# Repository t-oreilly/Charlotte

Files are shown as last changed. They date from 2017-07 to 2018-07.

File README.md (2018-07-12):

# Charlotte
Charlotte - Light Reactive Drawing Robot

Charlotte is an interactive drawing robot that senses light and responds to it accordingly.
Download the build instructions and STL files to build your own robot. Once compleated, you will be able to change the behavior
of the robot by uploading different codes. Watch a video of the robot in action here https://vimeo.com/221069279

You can also download the project from instrucables @ https://www.instructables.com/id/Charlotte/

Charlotte was first made in a http://schoolofma.org/ workshop in 2015

Collaborators 

Abe -  http://hamoid.com/ 

Peter Kolski 

Yuri - www.yurishimaoka.org

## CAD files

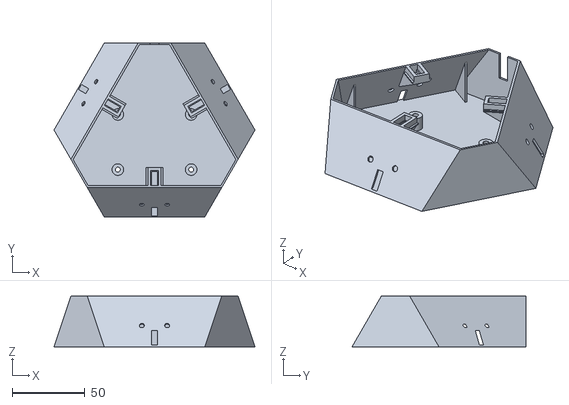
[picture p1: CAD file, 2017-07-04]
3::STL_/Body_1/mainBody_.stl
138.6 x 120.0 x 35.0

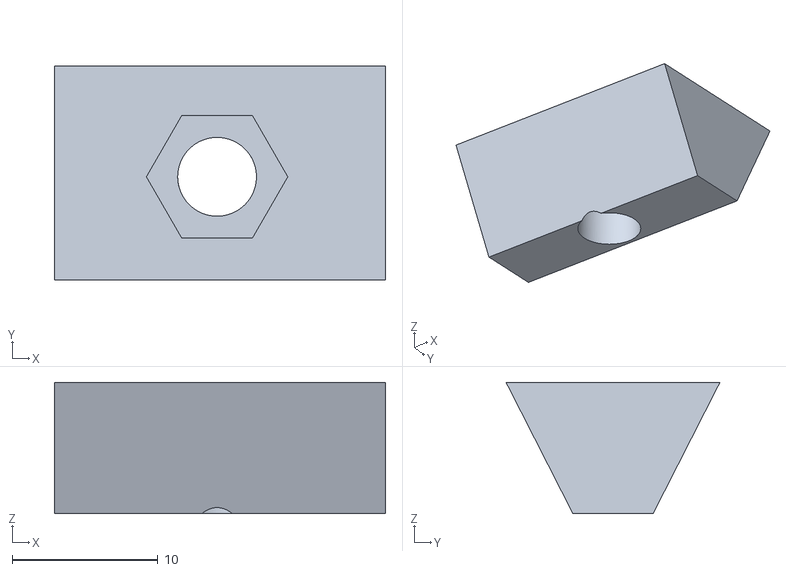
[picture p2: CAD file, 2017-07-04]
3::STL_/Body_1/servoWedge_.stl
22.7 x 14.7 x 9.00

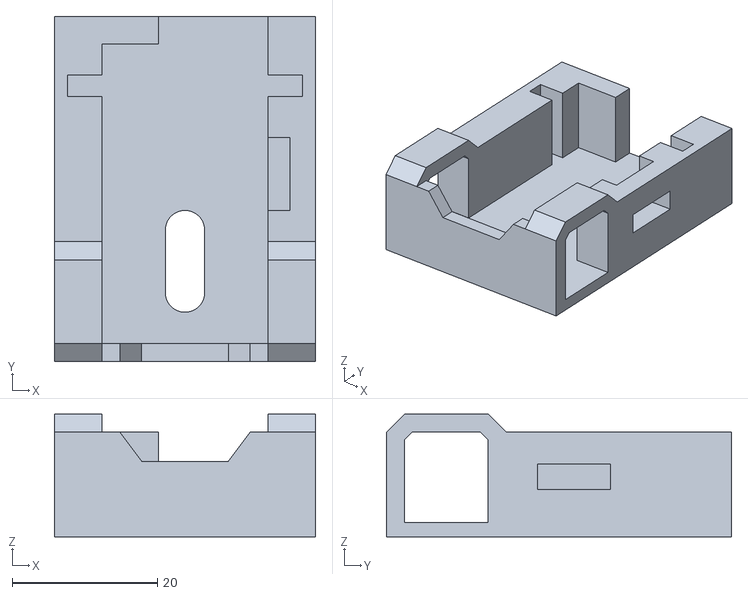
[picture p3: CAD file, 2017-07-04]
3::STL_/Body_1/servoHouseing_.stl
35.9 x 47.5 x 16.9

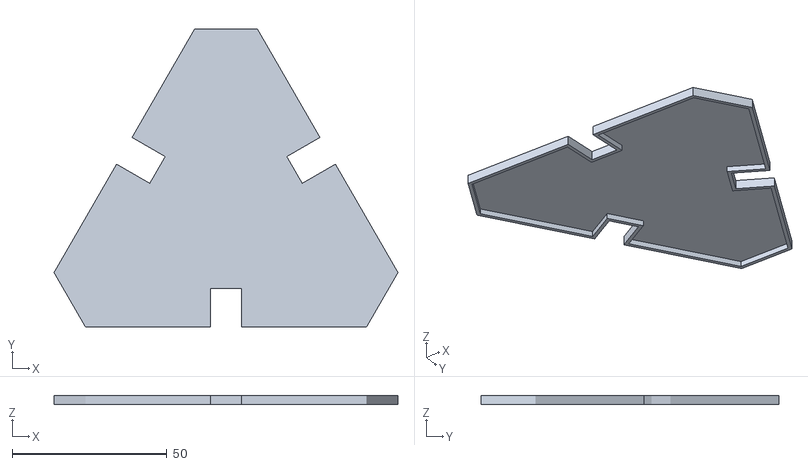
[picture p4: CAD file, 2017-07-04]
3::STL_/Body_1/bodyLid_.stl
111.3 x 96.4 x 3.00

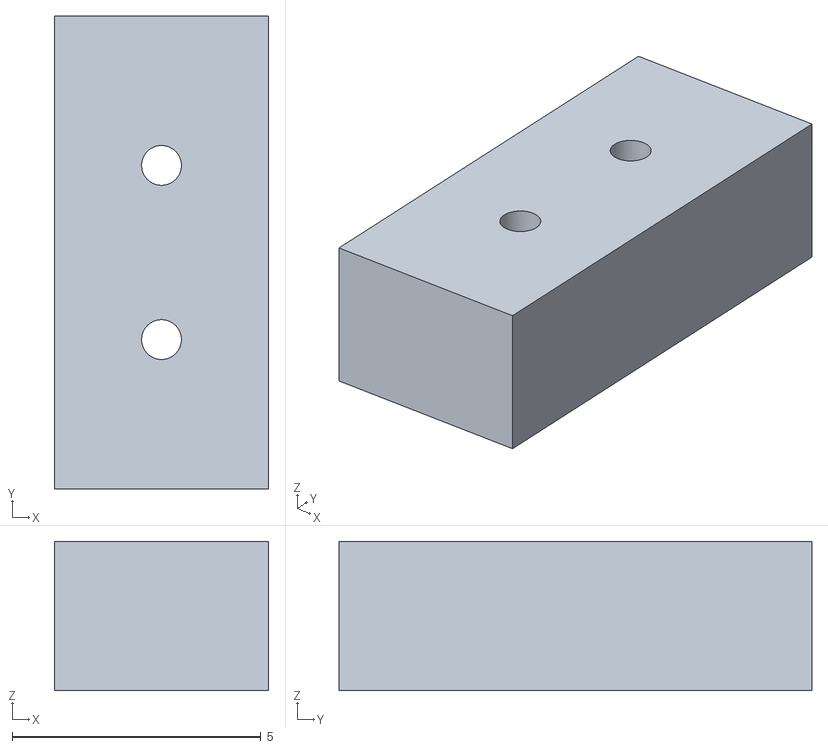
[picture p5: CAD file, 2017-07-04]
3::STL_/Body_1/sensorHouse_.stl
4.30 x 9.50 x 3.00

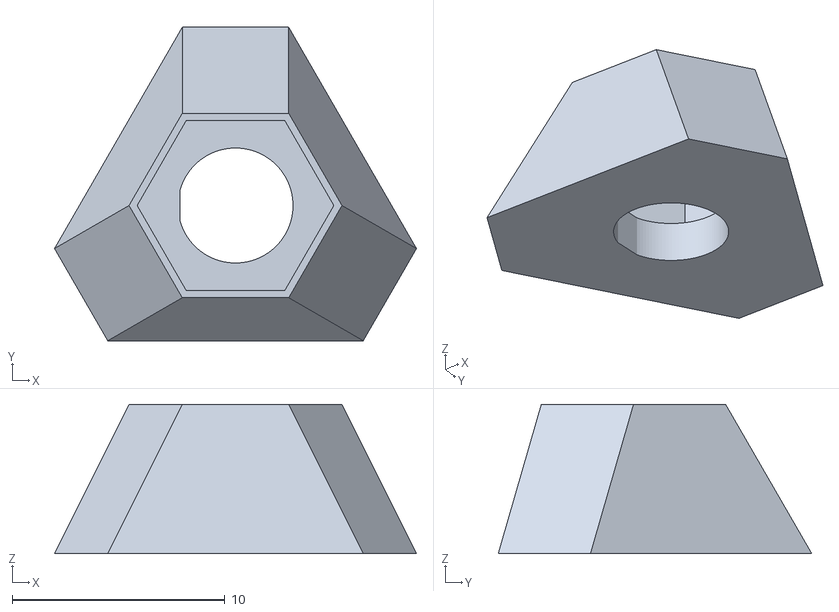
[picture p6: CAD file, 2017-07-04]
3::STL_/Body_1/boltHouse_.stl
17.0 x 14.7 x 7.00

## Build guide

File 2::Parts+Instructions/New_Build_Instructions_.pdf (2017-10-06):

Intro
Tools Needed
Parts Needed
Soldering

1
2
3
4
5
6
7

Callibration
Assembly
Play

### What if you could download a Product?

INTRO

The rise in popularity of 3D printing and the Internet becoming ubiquitous has prompted many speculations about how the democratization of manufacturing and the free sharing of information will affect our environments. Charlotte, as well as being a functional experience-focused robot, is one of those speculations. Being open sourced and transparent, it questions the binary relationship between manufacturer and consumer, encouraging modification over dictation.

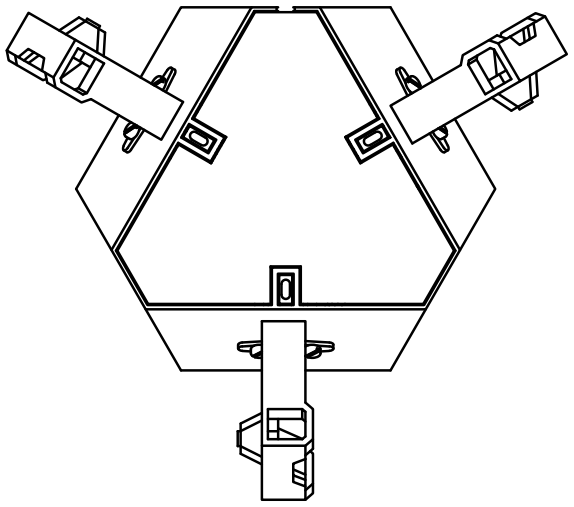
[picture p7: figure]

Charlotte’s movements are determined by light interpreted through three sensors located on top of its body. For legs, it has three pens that individually attach to form a tripod. Each light sensor controls the movement of one leg that marks the paper with every act.

### You Will Need:

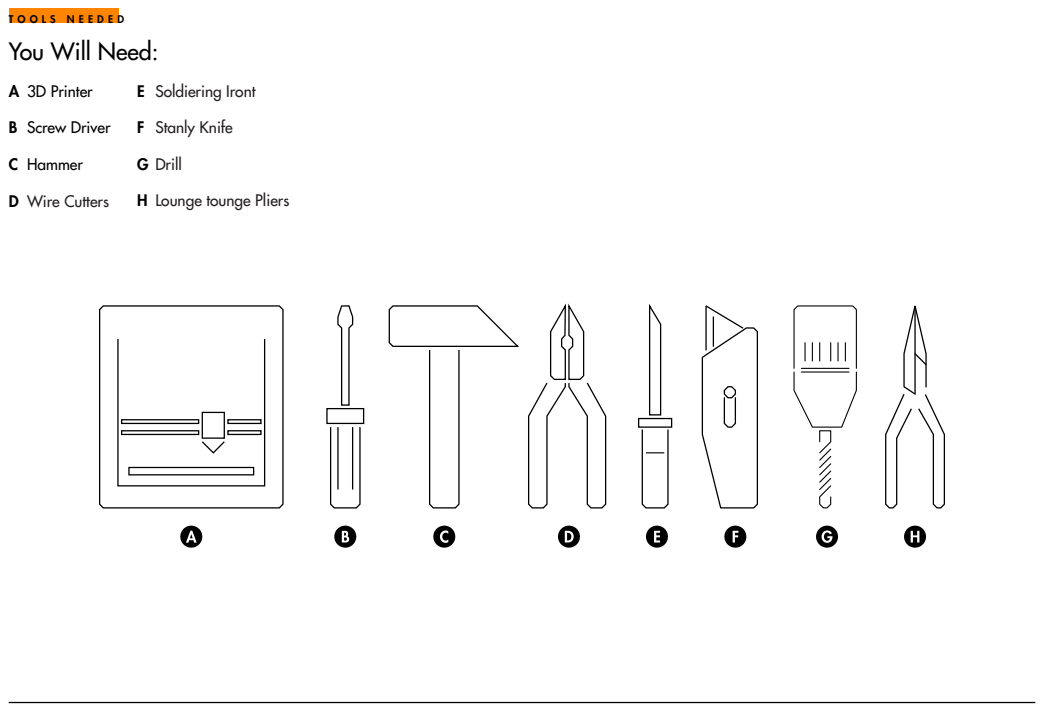
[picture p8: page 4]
TOOLS NEEDED; Wire Cutters; Screw Driver; Hammer; A 3D Printer

E Soldiering Iront
F Stanly Knife
G Drill
H Lounge tounge Pliers

### 3D Printed Parts/Laser Cut

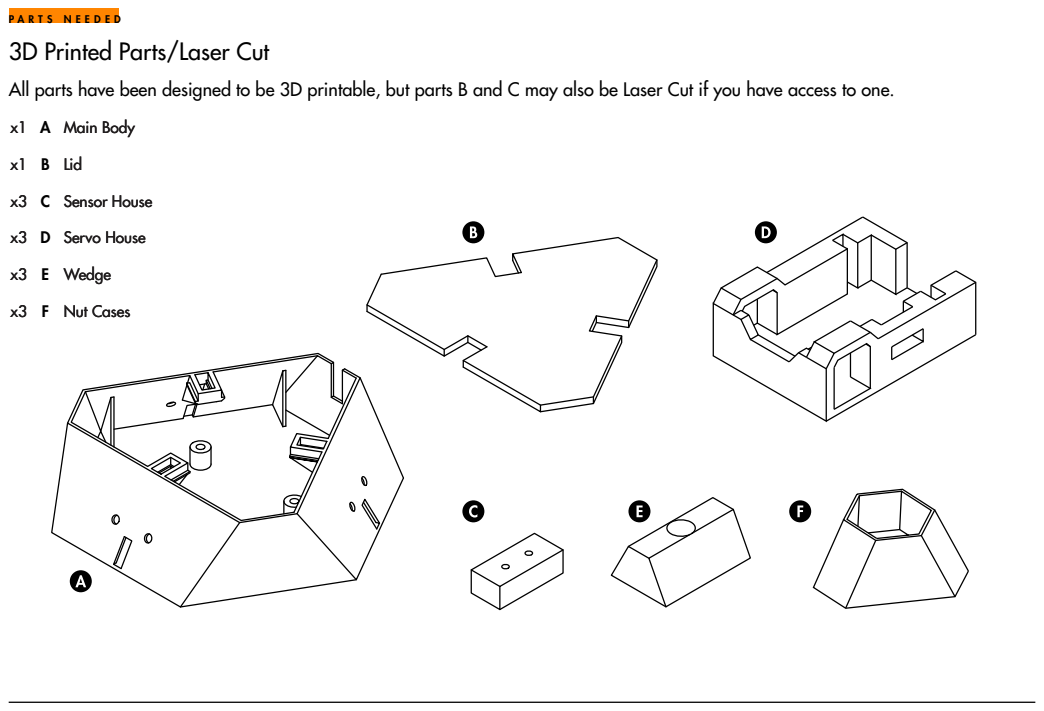
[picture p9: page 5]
PARTS NEEDED; Main Body; Wedge; Nut Cases; Servo House; Sensor House; Lid

All parts have been designed to be 3D printable, but parts B and C may also be Laser Cut if you have access to one.

### Electronic Parts

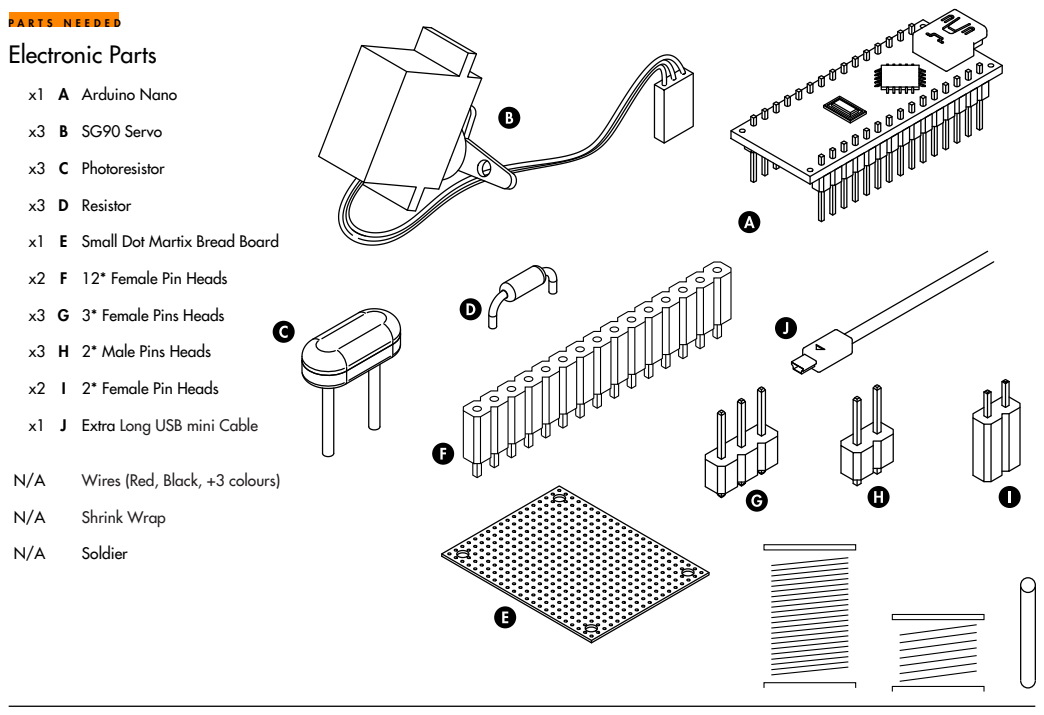
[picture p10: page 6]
PARTS NEEDED; Shrink Wrap; Wires (Red, Black, +3 colours); SG90 Servo; Photoresistor; Small Dot Martix Bread Board; 12* Female Pin Heads; 3* Female Pins Heads; 2* Male Pins Heads; Resistor; Arduino Nano; Extra Long USB mini Cable; Soldier; 2* Female Pin Heads

### Nuts,Bolts & Washers

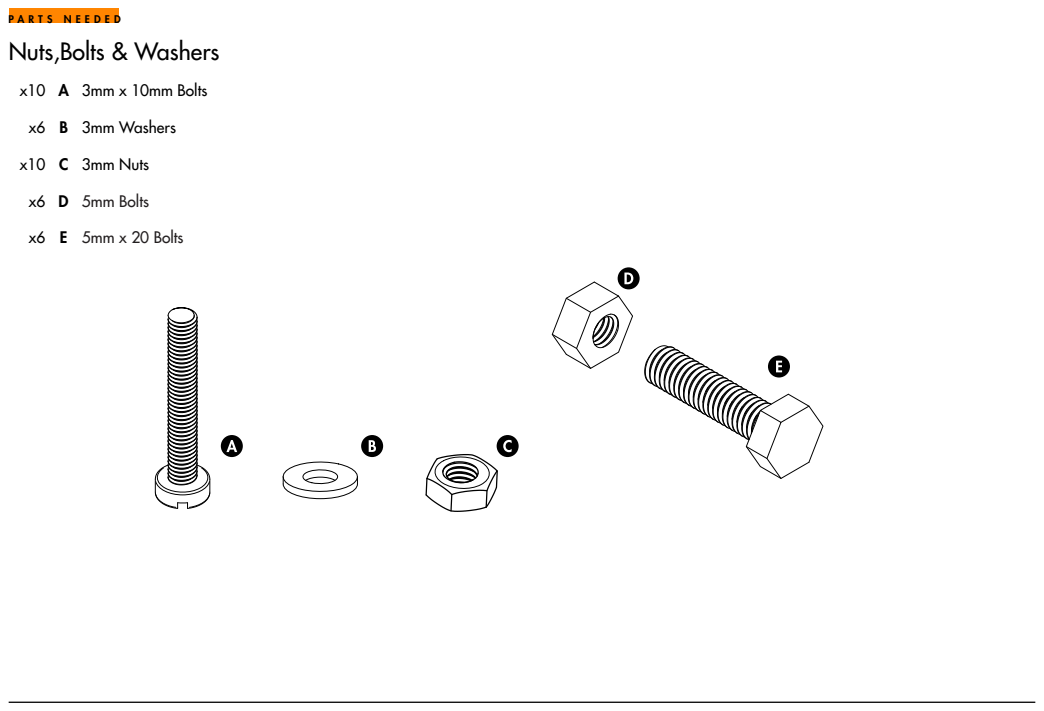
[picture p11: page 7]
PARTS NEEDED; 5mm Bolts; 3mm Washers; 3mm Nuts; x10 A 3mm x 10mm Bolts; E 5mm x 20 Bolts

### Solder

### Callibrate

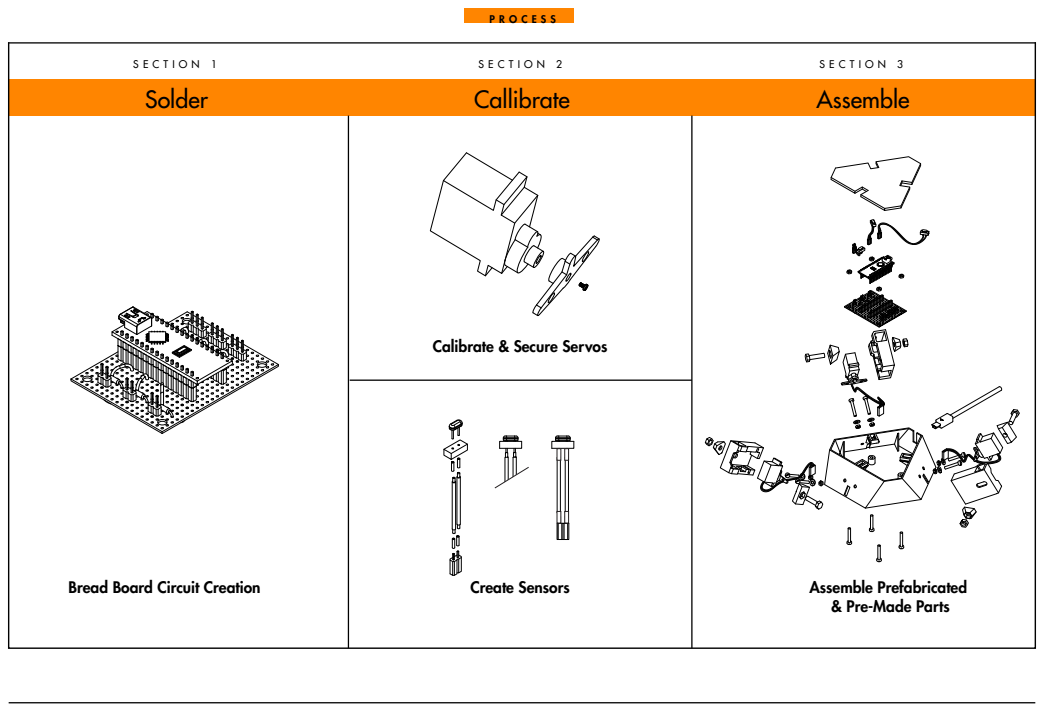
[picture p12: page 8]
PROCESS; SECTION 1; SECTION 2; Assemble; SECTION 3; Bread Board Circuit Creation; Create Sensors; Assemble Prefabricated

Calibrate & Secure Servos

& Pre-Made Parts

### Schematic

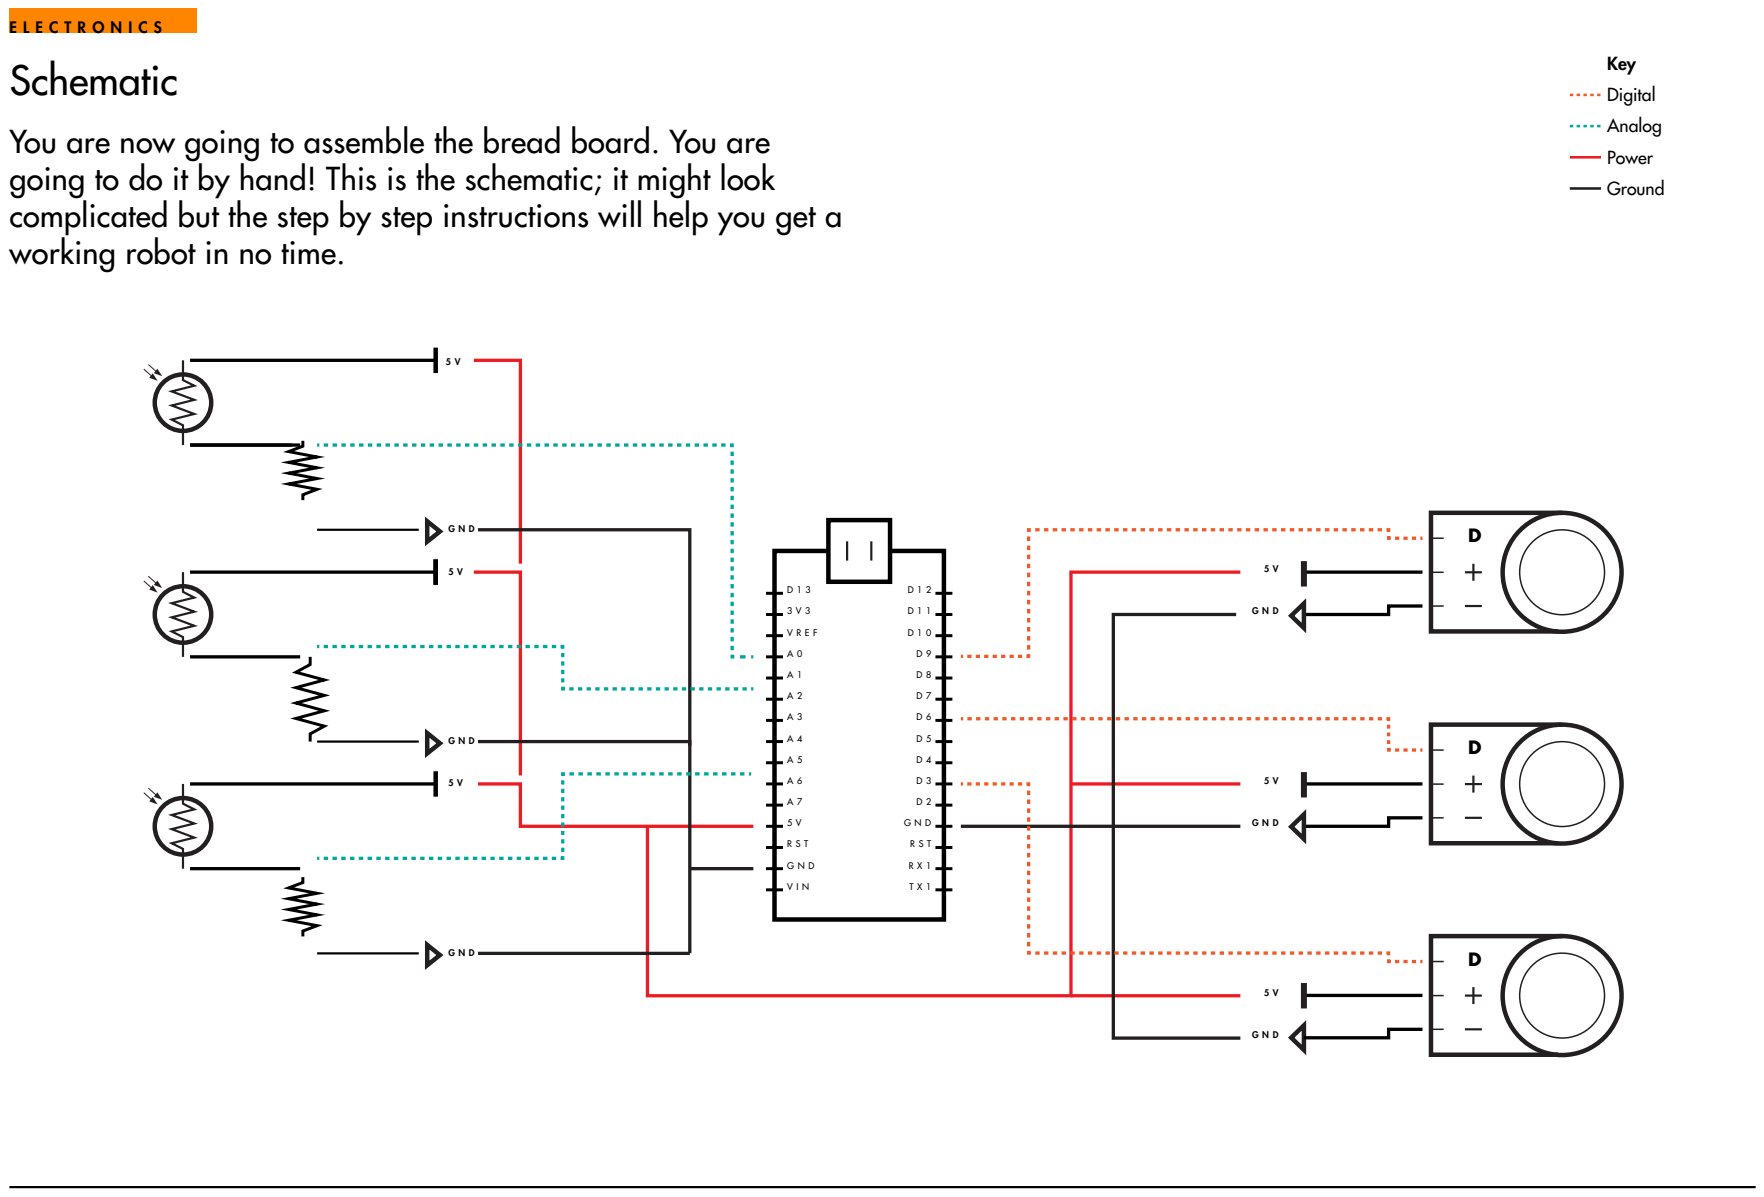
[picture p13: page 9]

You are now going to assemble the bread board. You are
going to do it by hand! This is the schematic; it might look
complicated but the step by step instructions will help you get a
working robot in no time.

### Bread Board

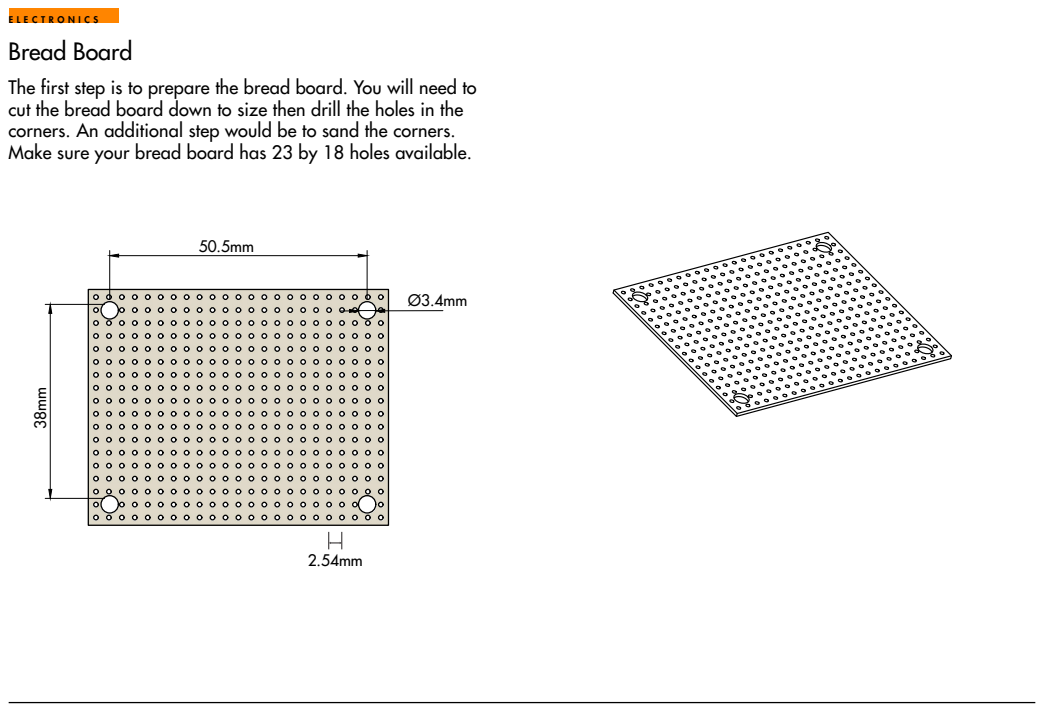
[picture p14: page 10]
ELECTRONICS

The first step is to prepare the bread board. You will need to
cut the bread board down to size then drill the holes in the
corners. An additional step would be to sand the corners.
Make sure your bread board has 23 by 18 holes available.

### Pins and Resistors

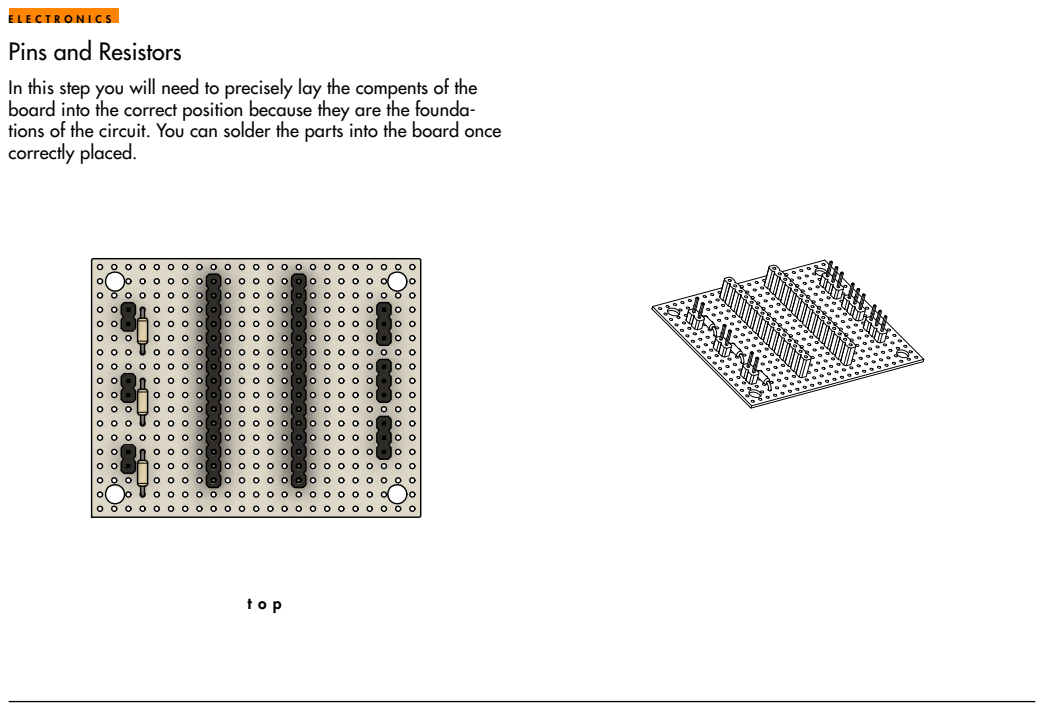
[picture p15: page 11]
ELECTRONICS; top

In this step you will need to precisely lay the compents of the
board into the correct position because they are the founda-
tions of the circuit. You can solder the parts into the board once
correctly placed.

### Arduino

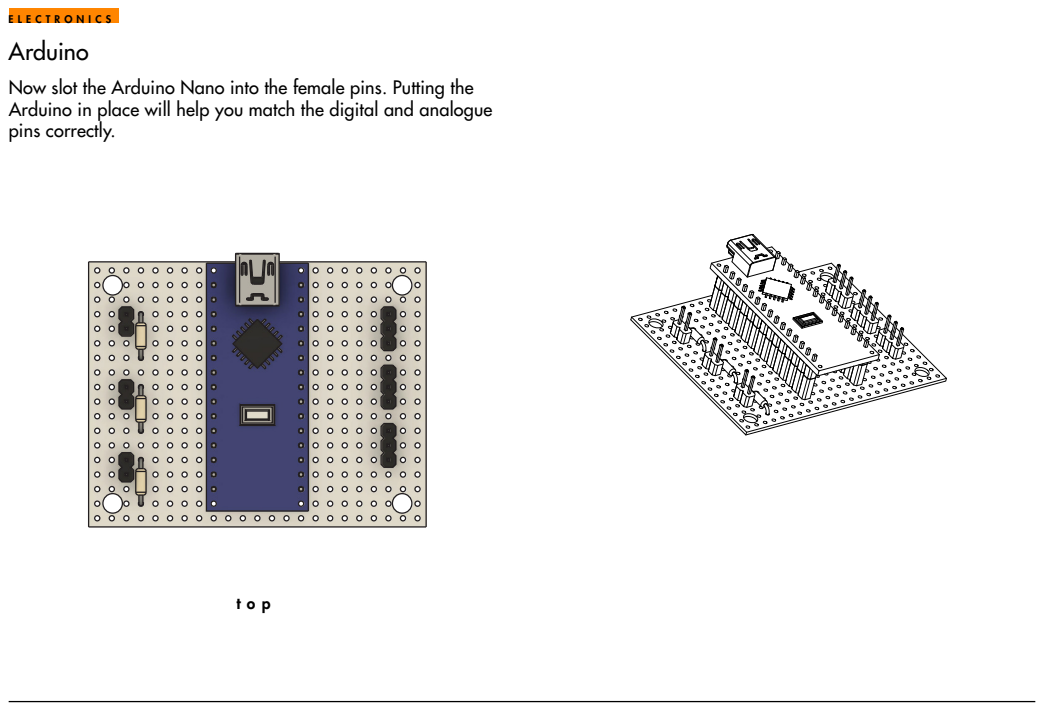
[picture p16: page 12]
ELECTRONICS; top

Now slot the Arduino Nano into the female pins. Putting the
Arduino in place will help you match the digital and analogue
pins correctly.

### Top Wires

Now solder in the digital and analog wires. Make sure that you
couple the digital pins D3, D6 and D9 and analog pins A0, A3
and A6 for they will be specifically referenced in the code that
you upload later.

### Connect Ground

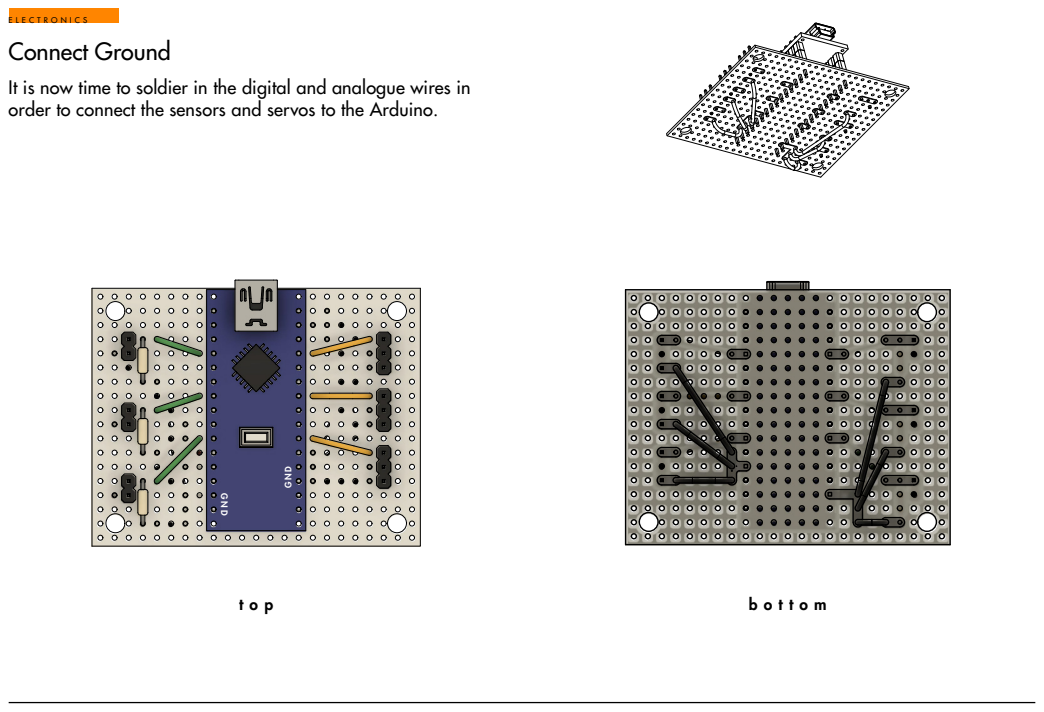
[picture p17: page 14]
ELECTRONICS; GND; top; bottom

It is now time to soldier in the digital and analogue wires in
order to connect the sensors and servos to the Arduino.

### Connect Power

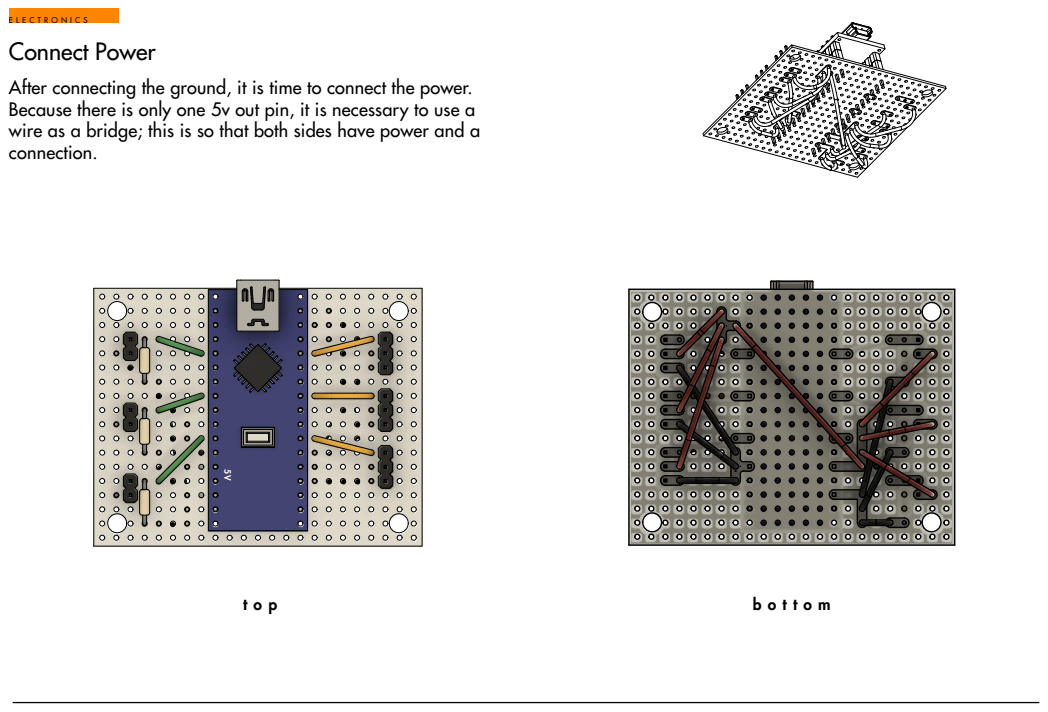
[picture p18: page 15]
ELECTRONICS; top; bottom

After connecting the ground, it is time to connect the power.
Because there is only one 5v out pin, it is necessary to use a
wire as a bridge; this is so that both sides have power and a
connection.

Drill two wholes into the Servo Horn, exactly 7.5 mm apart from each other. Use a 3mm drill piece. Use the plastic dots on the Servo Horn as reference.

Suggestion
Use double sided tape to stick Servo Horn to cardboard/MDF before drilling. Practice drilling on the spare Servo Horns that comes with all SG90 servos.

### Servo Drill

CALLIBRATE

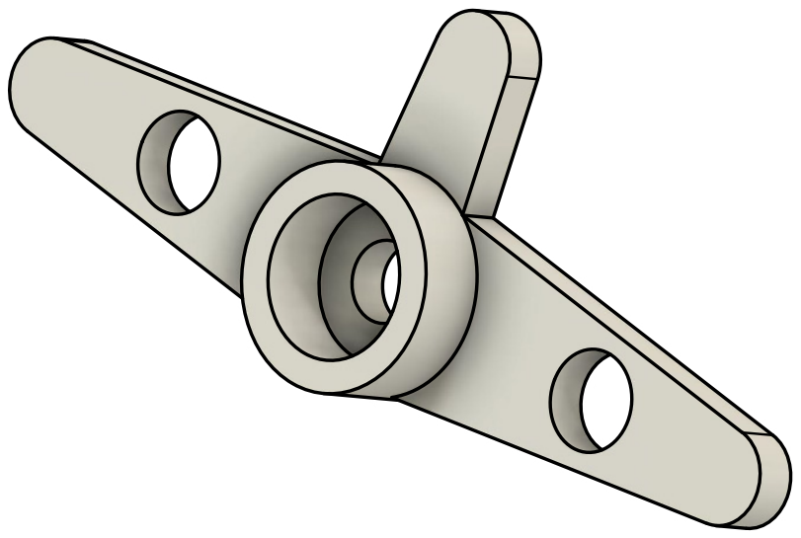
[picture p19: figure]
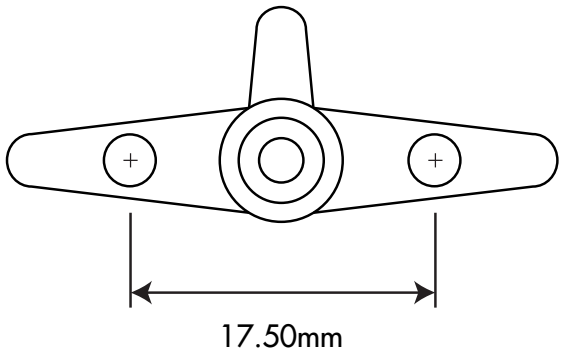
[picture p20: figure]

### Callibrate Servos

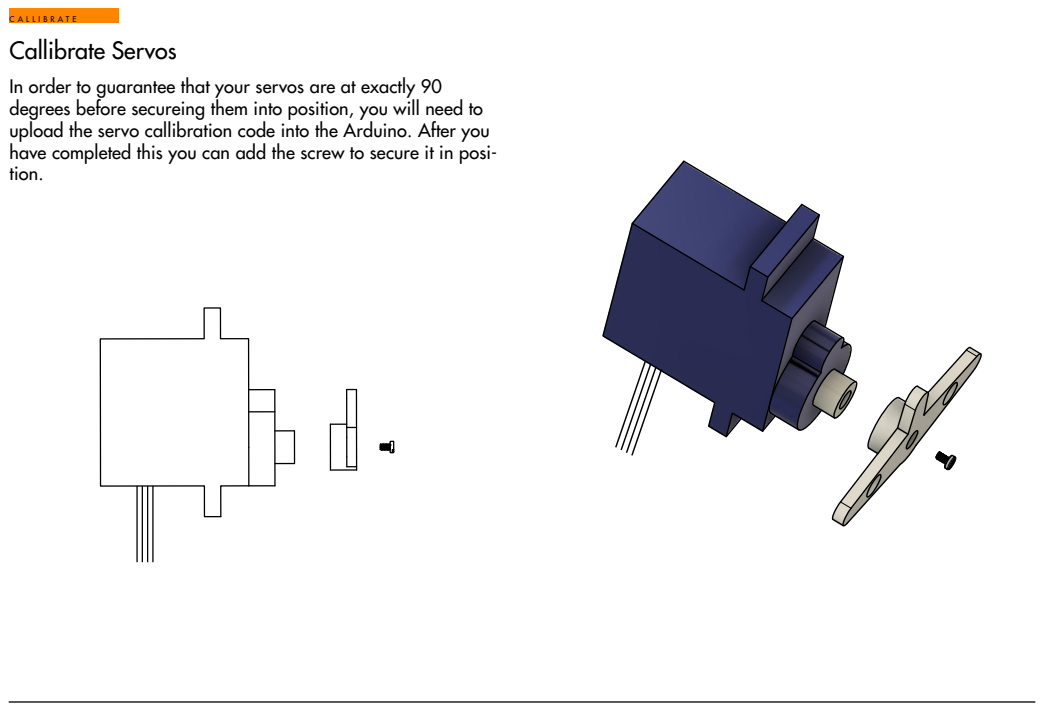
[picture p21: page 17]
CALLIBRATE

In order to guarantee that your servos are at exactly 90
degrees before secureing them into position, you will need to
upload the servo callibration code into the Arduino. After you
have completed this you can add the screw to secure it in posi-
tion.

### Create Sensors

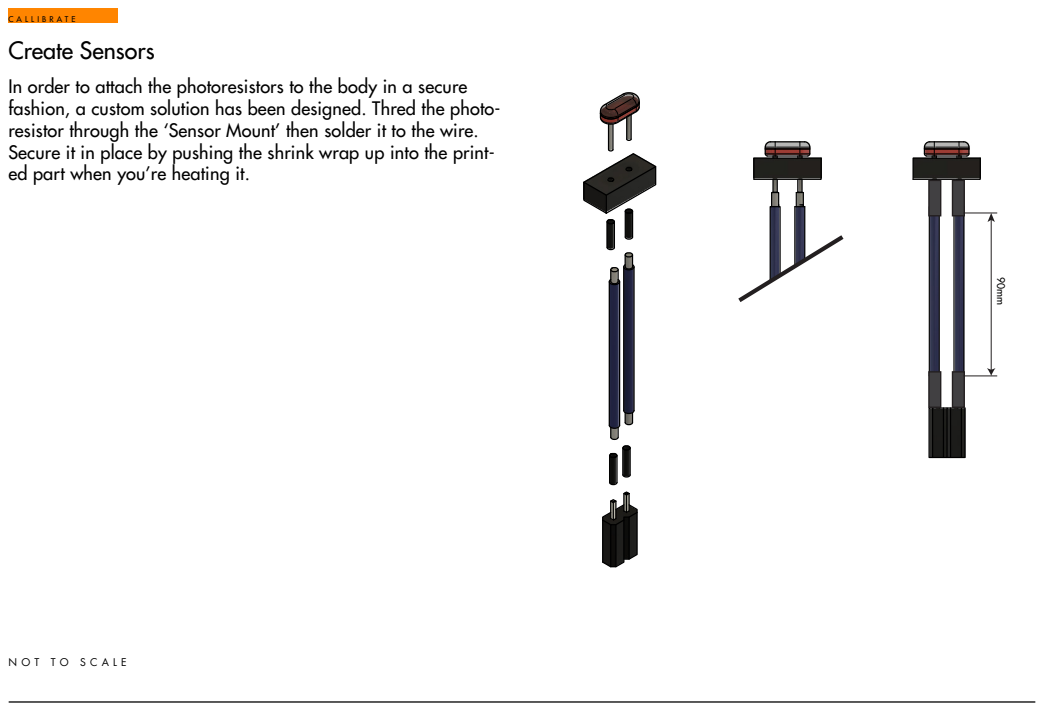
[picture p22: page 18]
CALLIBRATE

In order to attach the photoresistors to the body in a secure
fashion, a custom solution has been designed. Thred the photo-
resistor through the ‘Sensor Mount’ then solder it to the wire.
Secure it in place by pushing the shrink wrap up into the print-
ed part when you’re heating it.

NOT TO SCALE

### Attatch Servos

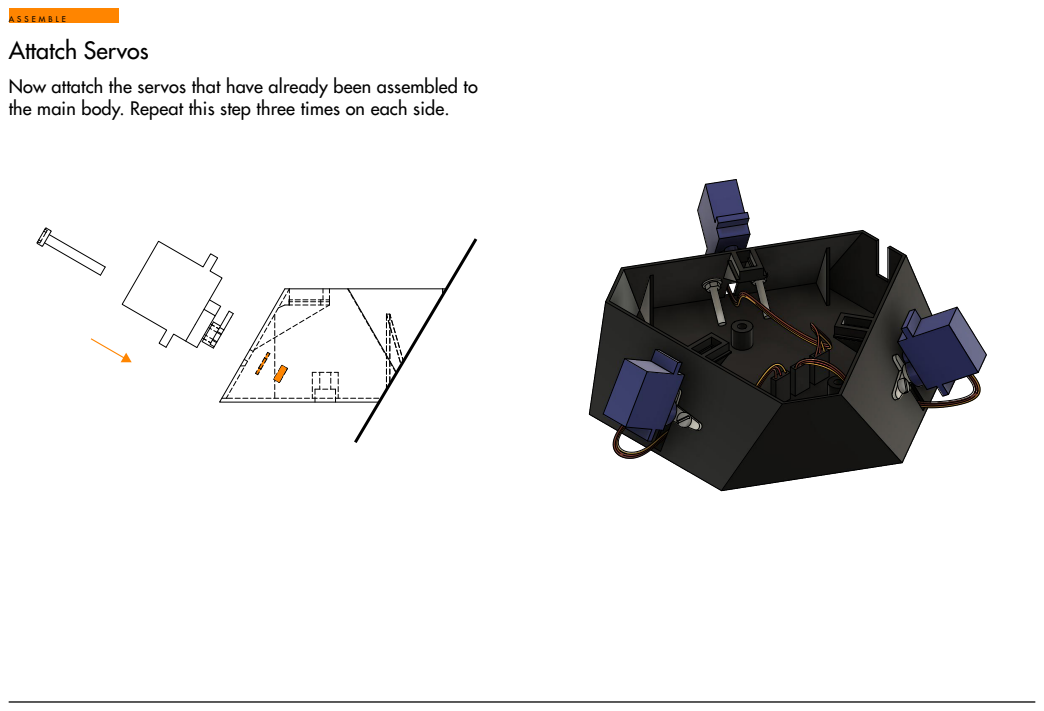
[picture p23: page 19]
ASSEMBLE

Now attatch the servos that have already been assembled to
the main body. Repeat this step three times on each side.

### Mount Electronics

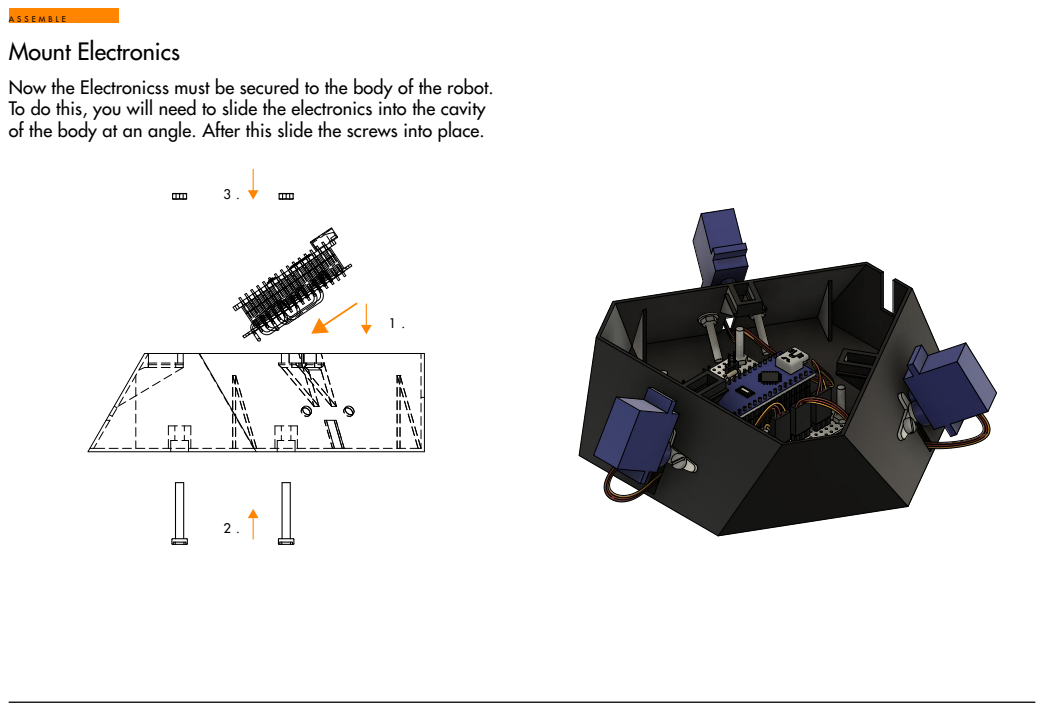
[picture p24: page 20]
ASSEMBLE

Now the Electronicss must be secured to the body of the robot.
To do this, you will need to slide the electronics into the cavity
of the body at an angle. After this slide the screws into place.

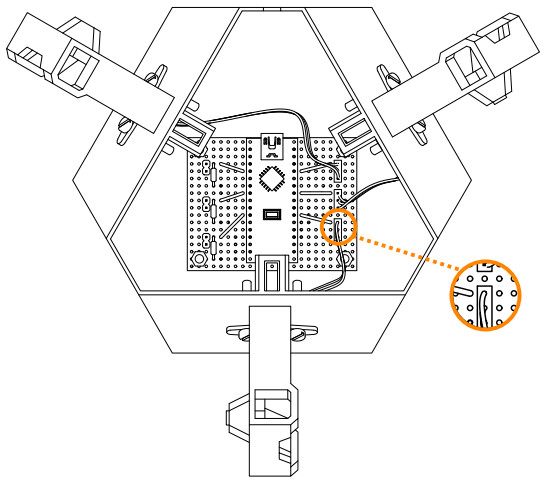
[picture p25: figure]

The first step is to thread the plastic female Pins through the hole in the bottom of the ‘Servo Housing.’ Now thread through the hole on the side of the body of the robot. You will then be able to plug the servo into its corrosponding male pins. Make sure you marry the digital pin on the servo with the digital pin on the bread board. After this you will be able to press the Servo housing onto the servo (do not worry if it appears loose because everything will be tightened when the pen is inserted and wedge tightend). Then you can attatch the rest of the parts as displayed in the diagram.

### Attatch Servo Housing

ASSEMBLE

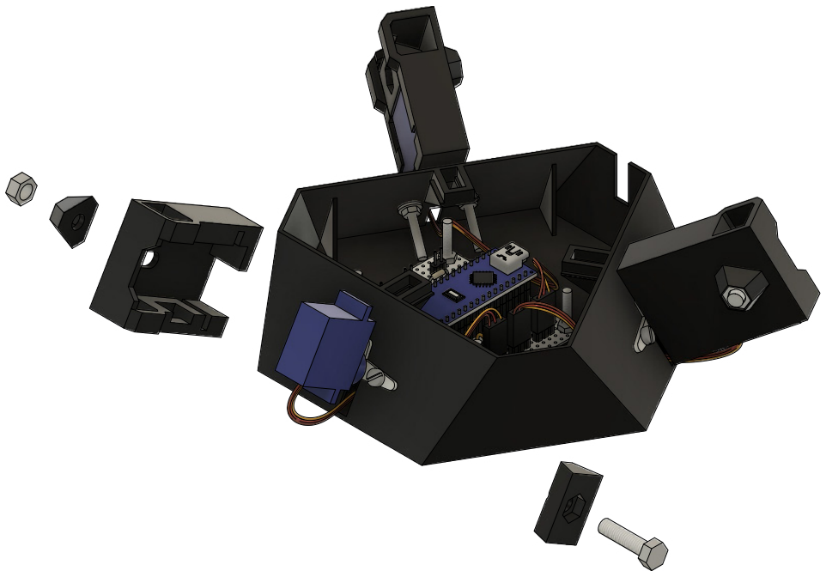
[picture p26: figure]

### Insert Sensors

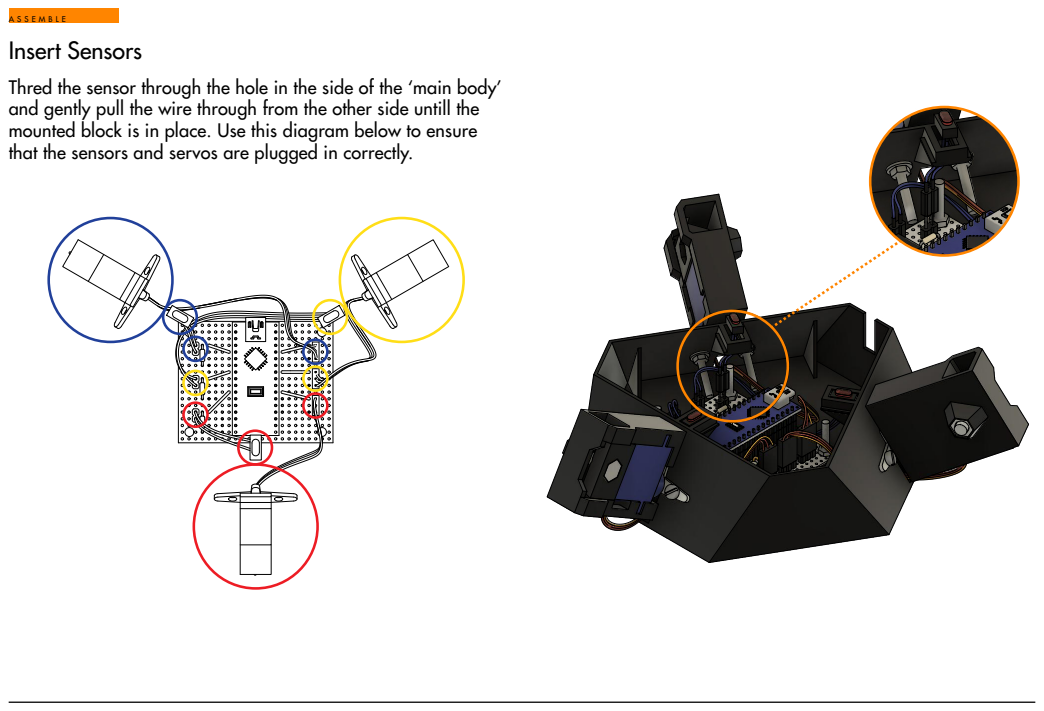
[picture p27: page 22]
ASSEMBLE

Thred the sensor through the hole in the side of the ‘main body’
and gently pull the wire through from the other side untill the
mounted block is in place. Use this diagram below to ensure
that the sensors and servos are plugged in correctly.

### Lid + Power supply

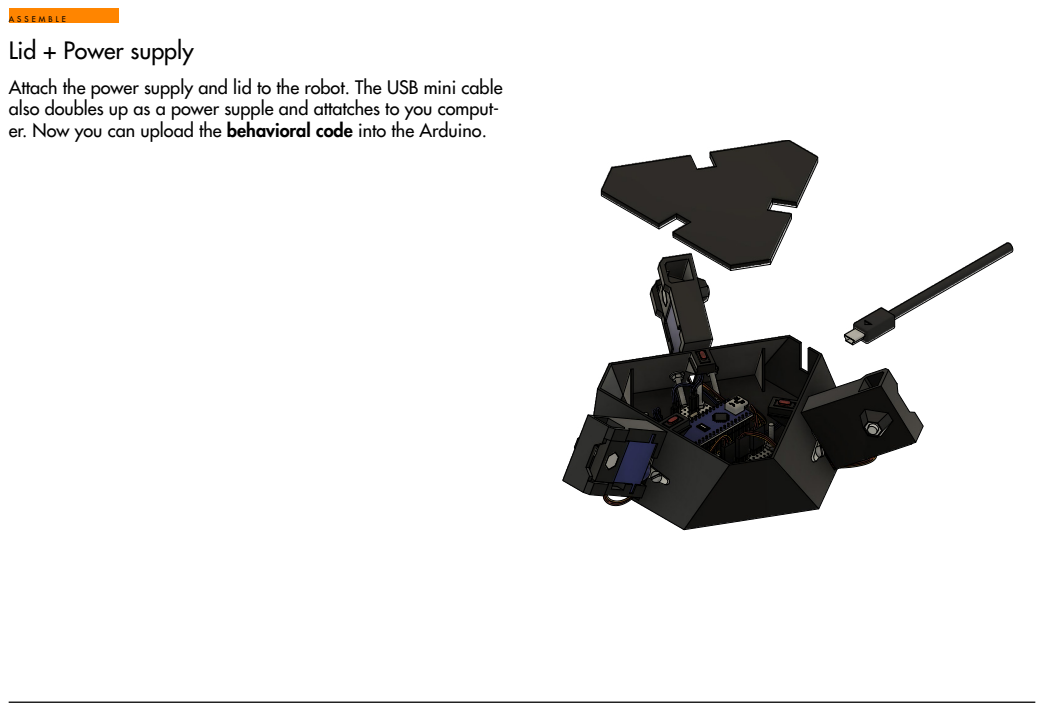
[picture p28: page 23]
ASSEMBLE

Attach the power supply and lid to the robot. The USB mini cable
also doubles up as a power supple and attatches to you comput-
er. Now you can upload the behavioral code into the Arduino.

### Insert Pens for Legs

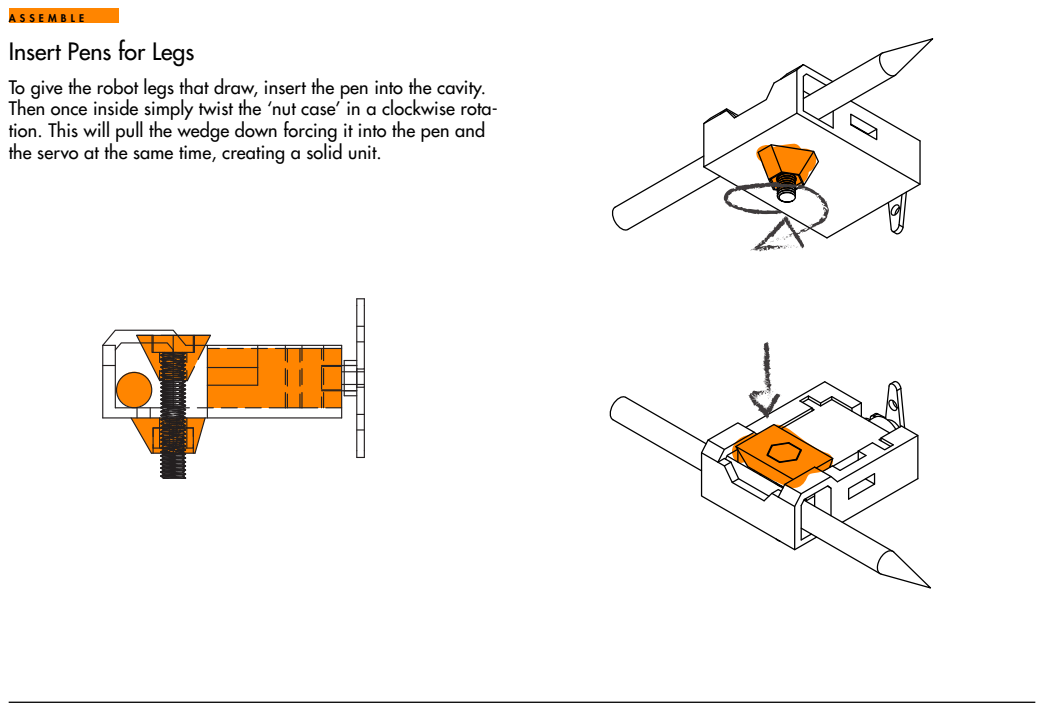
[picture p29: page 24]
ASSEMBLE

To give the robot legs that draw, insert the pen into the cavity.
Then once inside simply twist the ‘nut case’ in a clockwise rota-
tion. This will pull the wedge down forcing it into the pen and
the servo at the same time, creating a solid unit.

### Insert Pens + Explore!

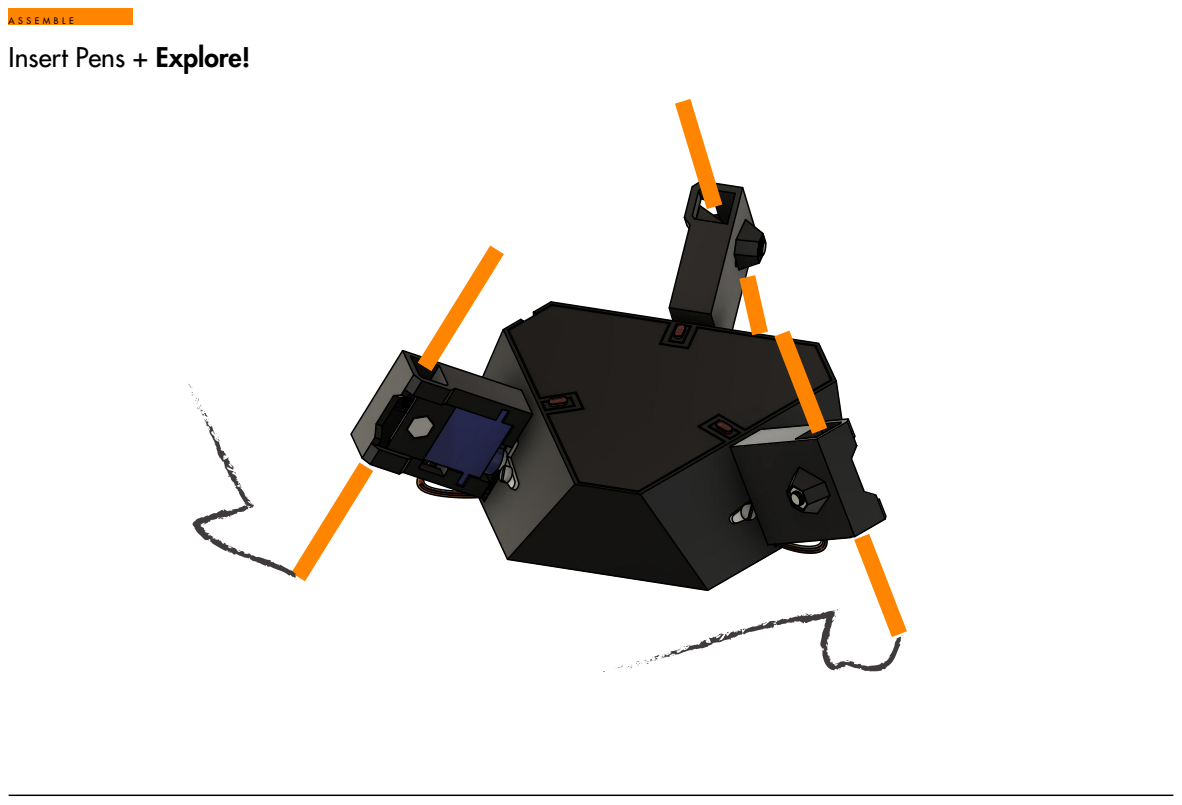
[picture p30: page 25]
ASSEMBLE

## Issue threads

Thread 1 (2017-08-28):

typo (ardunio vs arduino)

hamoid, 2017-08-28:
In the PDF file :)

t-oreilly, 2017-08-30:
oops!
Look I made PCBs :)
Also, I put the project on instructables -
https://www.instructables.com/id/Charlotte/

[image: Inline images 1]

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

--

Thomas O'Reilly
www.toreilly.com

t-oreilly, 2017-10-06:
dysxelia :)

t-oreilly, 2017-10-06:
the eternal excuse !

t-oreilly, 2017-10-06:
the eternal excuse !
